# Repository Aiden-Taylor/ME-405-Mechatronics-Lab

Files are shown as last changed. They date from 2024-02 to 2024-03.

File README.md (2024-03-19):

# ME 405 Term Project
### Authors: Aiden Taylor, Jack Foxcroft, Julia Fay
For our ME 405 term project we have designed a tracking and triggering system for a Nerf gun that utilizes two servo motors and a thermal camera to hit a target. These components were controlled by a Nucleo STM32L476 microcontroller, and the software was coded in Python and micropython. This design was to be used for educational purposes by students of ME 405. The purpose of the Nerf gun system was to participate in a duel against similar systems designed by classmates. Two participants were to stand behind their Nerf gun, move around for five seconds, and freeze while the opponent's gun tried to shoot them. Our system was ultimately successful in aiming, triggering, and hitting our opponent.

## Hardware and Mechanical Design
The turret hardware consists of a Nucleo STM32L476RG, and an adapter board, the “Shoe of Brian” which adds additional features to the Nucleo necessary for our project. To allow controlled actuation and triggering of the turret we employed two DC motors and encoders lent to us by the ME 405 lab and an infrared camera to sense the thermal signature of our target and calculate the setpoint for our aiming motor.
The mechanical design consists of 3D-printed gears, bearings, a baseplate, motor mounts, and a fixture to house the Nerf gun. The CAD model of the system is shown below with details regarding each component of the system and their purpose.

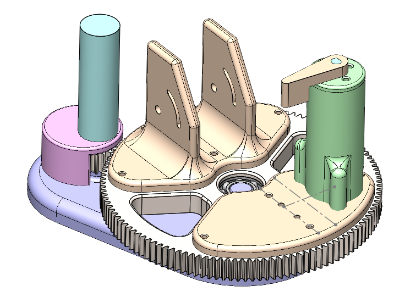
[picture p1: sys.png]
mechanical


**Figure 1:** Turret CAD Model

The gear ratio of our system is 6:1 and was designed to allow the turret to spin 180 degrees in one second. Overall, our design was made to be as simple and compact as possible while still being able to meet the requirements of the project.

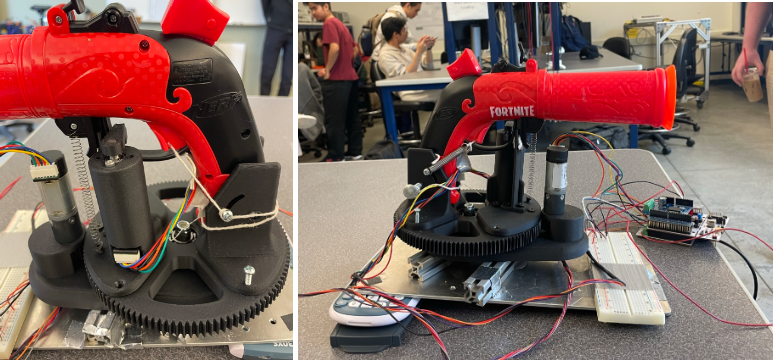
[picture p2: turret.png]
irlsys


**Figure 2:** Fully assembled turret with aiming and triggering subsystems.

To aid in providing the necessary force to engage the trigger mechanism, the team added a spring-tensioned string through the bottom portion of the trigger. Thus, when the servo moved the triggering lever, the trigger would engage consistently. A barrel support piece was added to aid in the gun's stability. Another spring was used to keep the gun secured on this support piece as seen in the left image above.

## Software Overview
The software for controlling the turret system was written in micropython such that it could be uploaded and run on the Nucleo. The team used a priority scheduler to efficiently run each task in the order of most time-sensitive to least time-sensitive. A generator function was used to generate effective multitasking between different system tasks. An in-depth coverage of the software can be found at the Doxygen page for this project https://aiden-taylor.github.io/ME-405-Mechatronics-Lab/

## Results
Our design was successful in tracking a target and shooting them after 5 seconds of the duel being initiated. However, we only produced this result once during our duel. We ran into some issues with the hardware, such as the wiring getting caught in the gears during the duel. We also missed our target two times. We tested our system at multiple stages in the project. Before we tested our FSM on the fully built system, we used the motors with flywheel attachments in the lab to ensure we were getting the expected outcome. Once the two motors were properly operating, we built the whole system and tested the full operation. This stage of testing included tuning the values of Kp for both the panning motor and the trigger motor. We aimed to minimize overshoot for the panning motor and ensure a large enough PWM signal was being sent to the trigger motor. Additionally, we adjusted the calculation for getting the position of the target from the thermal camera's output and converting this to how many degrees to turn the panning motor. To do this, we had to take into account that the thermal camera was closer to the target than the gun, and thus had a different angular relationship to the target than the gun. Improvements that could be made to the system to yield a more consistent outcome will be discussed in the next section.

## Takeaways and Recommendations
Overall, this project was very informative in terms of how to effectively implement a FSM in Python while utilizing a priority scheduler. You have to make sure that the period of your tasks is less than the period specified in the scheduler to ensure the correct operation. Also, the priority of the tasks must be balanced such that each task will have the chance to run. Having too high of a priority for a task may result in that task being run exclusively. Also, the team learned how to currently utilize shares. To ensure only one value was stored in each of the queues, the queue was cleared, and then restored at each instance of using the queue. This allowed us to avoid issues with grabbing an incorrect previous value for a share. 

In terms of the mechanical design of the system, several things could be improved upon. The budget for our system led us to the use of 3D printed parts which was a limiting factor in the mechanical operation. We used PLA to print the baseplate and had permanent shafts designed into the part which sheared off immediately after assembling the gears. To better improve this we suggest making the shafts separate parts made of stronger materials less prone to shearing.

We also noticed that the system was very prone to high friction and thus responded slower to inputs from our controller. To decrease system friction we recommend using higher-performance bearings, steel shafts, higher tolerance manufacturing of the baseplate for center-to-center distance of the gears, and snap rings to retain the gears and ensure correct alignment.

The system was also prone to missing its target which was the cause of many different issues. In our duel, we had five chances to aim, trigger, and shoot our target. We only hit our target one out of the five times, the system missed its target twice, a piece of string used to pre-load the trigger caught in the gears, and our trigger motor wire caught in the gears. In order to remedy these issues we recommend implementing better and more organized wire/string management to ensure the gears are left free to spin. To solve the aiming issue we recommend creating a more robust process in setting up the turret’s initial position and angle as well as the camera position and angle in reference to the turret and target.

The triggering mechanism also had its fair share of issues, mainly stemming from the torque required to trigger the Nerf gun. We recommend either using some sort of mechanical leverage to trigger the gun or selecting a higher torque servo motor for triggering to increase the repeatability of this system.

One software system that would be really interesting to implement would be real-time tracking. Our system takes one image of the target and calculates a setpoint based on the distance to the target, and the image column that the target was identified in. However, this required us to take the image after the target had stopped moving (after the five seconds had elapsed) to make certain that the setpoint calculated was correct. If real-time tracking was implemented, we might be able to calculate new setpoints every second or quicker to trigger the Nerf gun before the 5 seconds were up.

## Task Diagram and FSMs
### Task Diagram
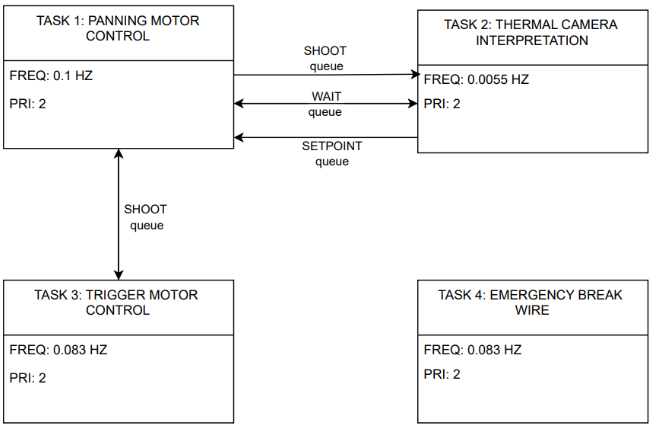
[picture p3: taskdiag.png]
tdiag


### Task 1 Finite State Machine
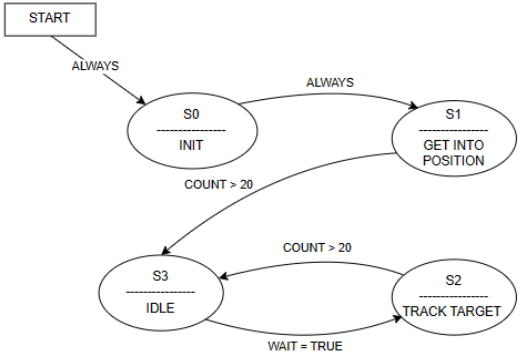
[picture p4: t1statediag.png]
t1diag


### Task 2 Finite State Machine
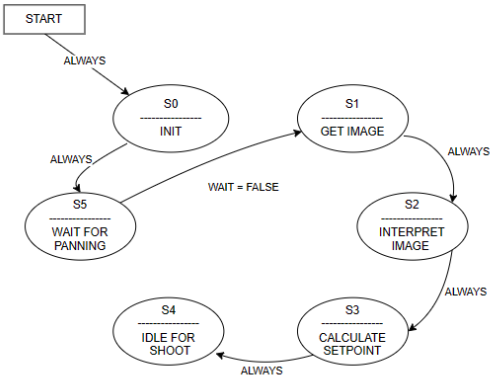
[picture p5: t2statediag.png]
t1diag


### Task 3 Finite State Machine
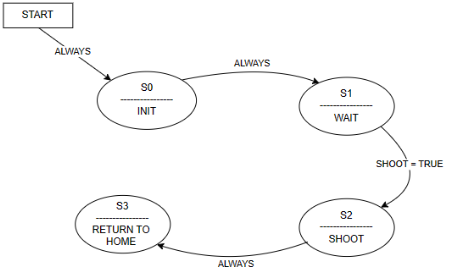
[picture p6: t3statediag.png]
t1diag


### Task 4 Finite State Machine
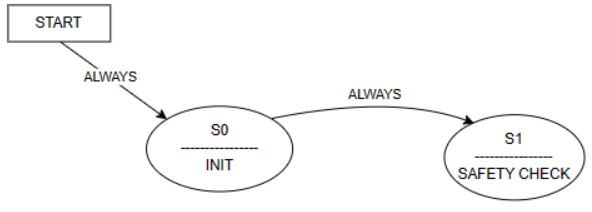
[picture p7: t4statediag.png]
t1diag


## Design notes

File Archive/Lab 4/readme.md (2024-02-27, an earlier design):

**README FOR THE BEST ME405 GROUP EVER**

*Authors: Aiden Taylor, Jack Foxcroft, Julia Fay*

~~Don't steal our code, or else you will be severly punished.~~

This GitHub is a compilation of all current code that has been written for ME405 Lab. The archive folder contains past lab code, while src contains the current lab's working code, the docs folder contains the documentation for the current lab, and the Doxyfile contains the Doxygen configuration.

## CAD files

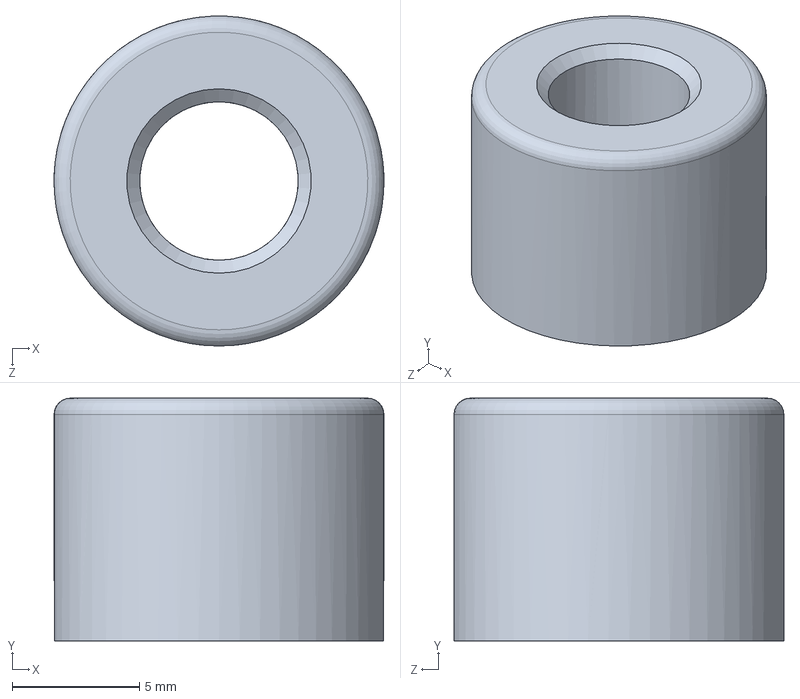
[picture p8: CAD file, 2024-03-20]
CAD/shaft.SLDPRT
13.0 x 9.53 x 13.0 mm

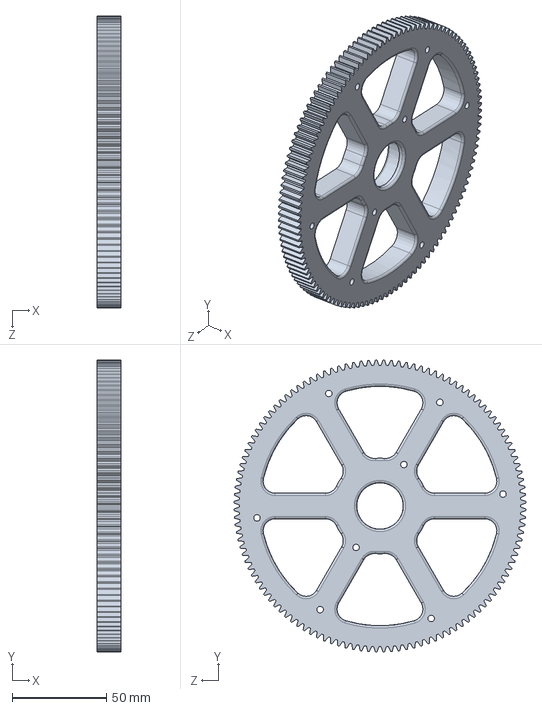
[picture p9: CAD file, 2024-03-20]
CAD/spur gear.SLDPRT
12.7 x 154.9 x 154.9 mm

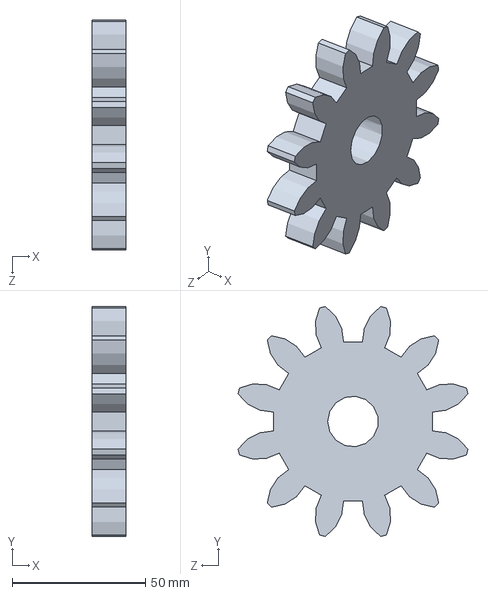
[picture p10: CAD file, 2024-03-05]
CAD/pinion.SLDPRT
12.7 x 86.4 x 86.4 mm

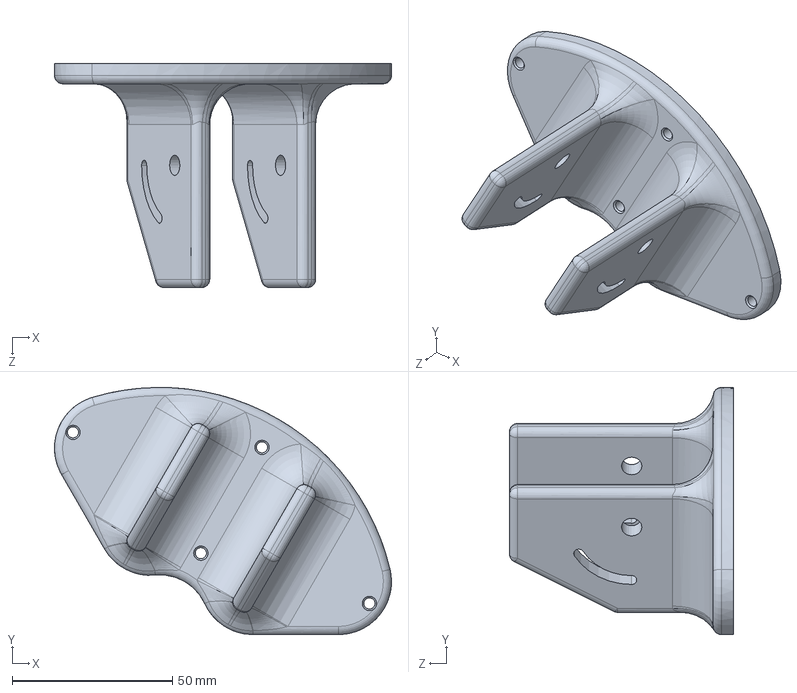
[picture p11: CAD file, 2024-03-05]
CAD/gun mount.SLDPRT
105.0 x 77.0 x 69.8 mm

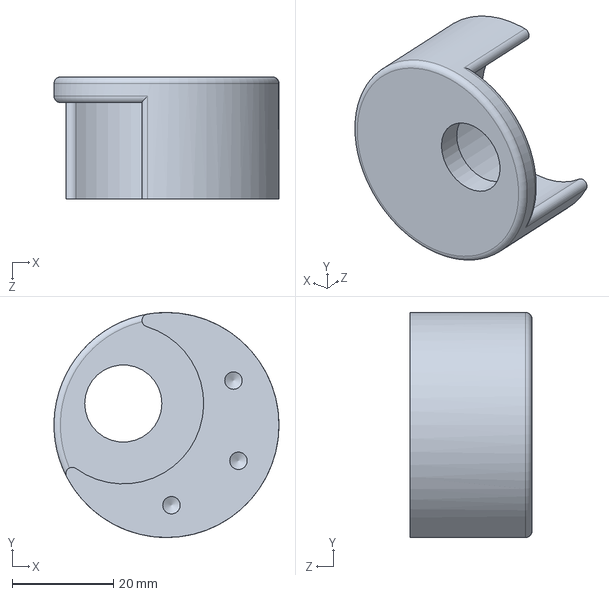
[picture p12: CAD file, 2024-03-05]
CAD/motor mount.SLDPRT
44.4 x 44.5 x 24.1 mm

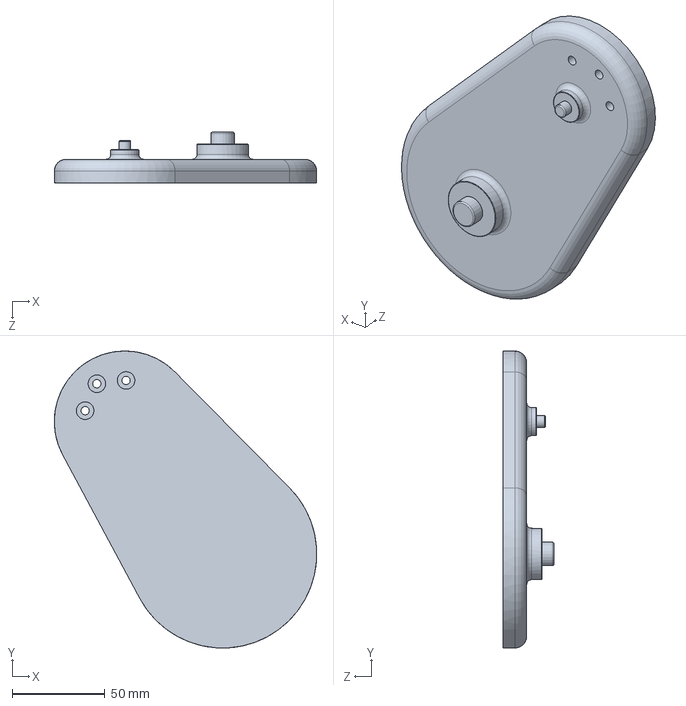
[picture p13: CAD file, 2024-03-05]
CAD/base.SLDPRT
141.7 x 160.4 x 27.3 mm

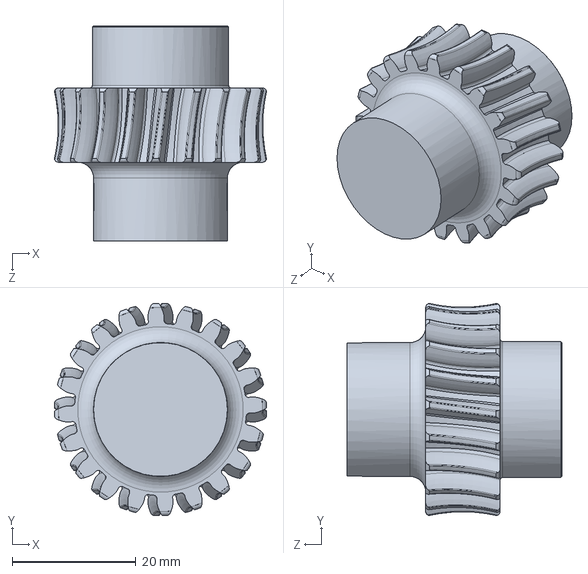
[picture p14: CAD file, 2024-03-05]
CAD/Part1.SLDPRT
34.2 x 34.2 x 34.7 mm

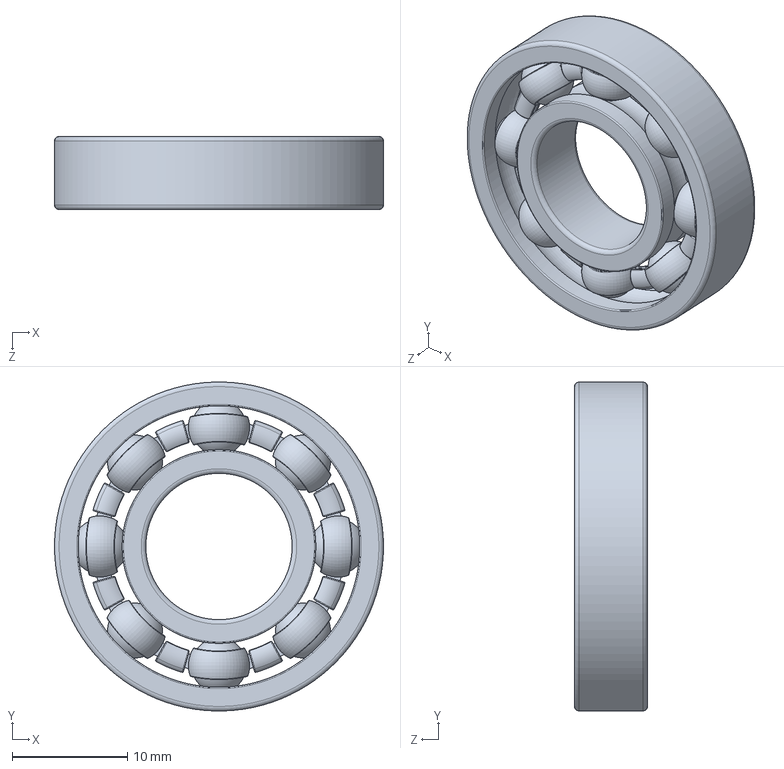
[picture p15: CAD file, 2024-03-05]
CAD/60355K173_Ball Bearing BIG.SLDPRT
28.6 x 28.6 x 6.35 mm

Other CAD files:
CAD/60355K173_Ball Bearing.SLDPRT

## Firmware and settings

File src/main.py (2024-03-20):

"""!
@mainpage Software Overview

@section intro_sec Introduction

This main page covers the workings of the main.py file used for this project, as well as the files that were used to make the whole system work.

@section file_sec Files

This is an overview of the files that we wrote and utilized:

@subsection controller_sec controller.py

This file is used as a high-level proportional controller for our motors. We use it to control the desired position of our motors, and also to interface with some of the lower-level files, seen below.

@subsection csv_sec csv_reader.py

This file was originally used for a plotter, but for the purposes of this project we adapted it to read the output of the thermal camera. We wrote a method in the class that reads the camera data, and then calculates the hottest thermal column, which is what we used to pick an aiming point.

@subsection encoder_sec encoder_reader.py

This file is a fairly self-explanatory class. We use it to read from the encoders and handle all the calculations related to determining the position of the motors. This file is referenced by the controller to read the motor positions.

@subsection mlx_sec mlx_cam.py

This is a file that was provided to us to read the infrared camera output. It was utilized in Task 2 of our main file.

@subsection motor_sec motor_driver.py

This file is used to control the speed of the motors. It takes a desired pwm output and feeds it to the motor driver. This file is also referenced by the controller, which uses this file and the encoder reader to create an effective proportional controller.

@section task_sec Tasks

IMAGE_PATH = my_image_dir

@image html taskdiag.png

The following are the tasks and states used in the main file of this project:

@subsection t1_sec Task 1

@image html t1statediag.png

Task 1 runs the panning motion for motor #1. This task first moves the turret into the 
    aiming position (180 degrees from initial position). Then, updates the panning motor 
    setpoint calculated by the thermal camera and runs until the PWM signal falls below 50%
    for more than 20 cycles and sets the panning motor duty cycle to 0 and waits for the trigger
    motor to complete its task. These are the states that are utilized in Task 1:

@subsubsection t1s0_sec State 0

This state is an initialization state for the panning motor that sets up the enable, pwm, and encoder pins, as well as
    establishing the controller class instance for the pan.

@subsubsection t1s1_sec State 1

This state is used to capture an image. Once that is completed, we move to state 2.

@subsubsection t1s2_sec State 2

This state is used when the turret is panning to track the target. In this current implementation of our code, we are not actively tracking 
    a target, we are instead waiting for the 5 seconds and then turning towards the target and firing. If we wanted to implement active
    tracking in the future, this state is ready for that, with a few modifications.

@subsubsection t1s3_sec State 3

This state is an idle for the panning motor. This is used both when we are tracking the duel target, and when we are waiting for our turret to fire



@subsection t2_sec Task 2

@image html t2statediag.png

Task 2 deals with the thermal camera. It initializes the camera's i2c communication
    protocal them waits until the panning motor completes its initial movement to the aiming position
    180 degrees from the initial postion. Then wait 3.25 seconds and get the image.
    Then, using the csv_reader class, calculate the column with the maximum summed thermal
    signature and calculate the setpoint based on the column. These are the states that are utilized in Task 1:

@subsubsection t2s0_sec State 0

This state is an initialization state for the camera that intitializes the mlx_cam class instance, as well as setting the refresh rate of the camera.

@subsubsection t2s1_sec State 1

This state is used to spin the whole turret 180 degrees at the start of the duel. Once it has turned, it switches to state 3.

@subsubsection t2s2_sec State 2

This state utilizes the csv reader to interpret the data that was captured by the camera in state 1. This gives us a column from the data that we need to
    aim at. This moves us to state 3.

@subsubsection t2s3_sec State 3

This state takes the data that we got from the csv reader and uses trigonometry and information about our camera and setup geometry to calculate the angle 
    that our turret needs to turn to correctly aim at the target, and then it uses a shared variable to pass that information to Task 1 and 3.
    
@subsubsection t2s4_sec State 4

This state waits for the turret to fire and does not take any images that may cause lag.

@subsubsection t2s5_sec State 5

This state waits for the panning motor to spin 180 degrees at the start of the duel before taking any images.

    
@subsection t3_sec Task 3

@image html t3statediag.png

Task 3 runs the trigger motion for the motor #2. First, task 3 waits until the panning
    motor reaches the setpoint calculated by the thermal camera. Then, it runs the trigger motor
    to a setpoint of 30 degrees, then returns to its intial position. The states it uses are below:

@subsubsection t3s0_sec State 0

This state is an initialization state for the trigger motor that sets up the enable, pwm, and encoder pins, as well as
    establishing the controller class instance for the trigger.

@subsubsection t3s1_sec State 1

This state is used to wait until the turret is ready to fire

@subsubsection t3s2_sec State 2

This state is used when the turret is firing. This activates the trigger motor to pull until it reaches the desired setpoint that we 
    tested to guarantee that the turret fires.

@subsubsection t3s3_sec State 3

This state returns the trigger mechanism to its zero location after firing.

@subsection t4_sec Task 4

@image html t4statediag.png

Task 4 is a simple task that acts as our safety system. Our design used a safety wire that when pulled, shuts down the whole system. The states used are as follows:

@subsubsection t4s0_sec State 0

This state simple initializes the variables used for the safety wire.

@subsubsection t4s1_sec State 1

This state is where the safety task always operates after initialization. It checks that the wire is still connected. If the wire is pulled, then the system is halted and will no longer
    operate until it is reset and the safety wire is replaced.

@file main.py

This is the main file for the term project. 

@author Aiden Taylor, Jack Foxcroft, Julia Fay
@date   2024-Mar-18
"""


#import all relevant modlues and files 
import gc
import pyb
import cotask
import task_share
import controller
import utime
import mlx_cam
import csv_reader
import math

#create global variable done 
global done
done = False 

def task1_fun(data):
    """!
    Task 1 runs the panning motion for motor #1. This task first moves the turret into the 
    aiming position (180 degrees from initial position). Then, updates the panning motor 
    setpoint calculated by the thermal camera and runs until the PWM signal falls below 50%
    for more than 20 cycles and sets the panning motor duty cycle to 0 and waits for the trigger
    motor to complete its task
    
    @param data The tuple used to store all shared variables between tasks
    """
    setpoint_share, shoot_share, wait_share = data  # Access shared variables from data tuple
    t1_state = 0; 
    
    print("Starting task 1")
    
    while True:
        

        shoot = shoot_share.get()  # Get shoot flag from shared variable
        wait = wait_share.get()
        wait_share.put(wait)
        
        # Implement FSM inside while loop
        #S0 - MOTOR INIT 
        #Initialize motor pins, Kp value, and position 
        if (t1_state == 0):
            # Run state zero code
            print("Task 1 state: ", t1_state)
            print("Initializing panning motor and encoder")
            ena = pyb.Pin.board.PC1
            in1 = pyb.Pin.board.PA0
            in2 = pyb.Pin.board.PA1
            motimer = 5

            #encoder init
            cp1 = pyb.Pin.board.PC6
            cp2 = pyb.Pin.board.PC7
            cptimer = 8
            Kp_init = 10
            setpoint = 0
            setp_init = 0       #   FIGURE OUT WHAT TO SET THIS TO FOR EACH MOTOR
      

            #establish controller object
            global var
            var = controller.P_Control(Kp_init, setp_init, 0, motimer, ena, in1, in2, cp1, cp2, cptimer)

            #zero the encoder count and position
            var.zero()
            var.set_Kp(Kp_init)
            global timtimeint
            timtimeint = utime.ticks_ms()
            var.moe.set_duty_cycle(0)
            #make sure the queue only has one value  
            wait_share.get()
            wait_share.put(True)
            count = 0

            #always go to state 1 from init  
            t1_state = 1   


        #S1 - GET INTO POSITION     
        elif (t1_state == 1):
            print("In the process of moving 180")
            #create the 180 degree setpoint (180 degrees, w/ a gear ratio of 6:1 so 6*180)
            one_eighty = 6*180
            var.run(one_eighty,timtimeint)
            print("Task 1 state: ", t1_state)
            
            #Check if the motor has reached this new position by checking if the PWM 
            #signal stays below 20 at least 10 times 
            if abs(var.get_PWM()) < 50:
                count += 1
            if count > 20: 
                print("I moved 180!")
                #turn off trigger motor
                var.moe.set_duty_cycle(0)
                #clear the queue and put False  
                wait_share.get()
                wait_share.put(False)
                #always go to the Idle state 3 to wait for the camera image to be taken 
                t1_state = 3
                #reset the count to zero 
                count = 0
                var.set_Kp(5)
                #zero the encoder position 
                var.zero()

        
        #S2 - TRACK TARGET    
        elif (t1_state == 2): 
            print("Task 1 state: ", t1_state)    
                    
            setpoint = setpoint_share.get()  # Get setpoint from shared variable
            setpoint_share.put(setpoint)     # Make sure the queue stays neutral
            print(f"updating setpoint is: {setpoint}")
           
            #update the motors setpoint and run 
            var.run(setpoint, timtimeint)
            
            #Check if the motor has reached this new position by checking if the PWM 
            #signal stays below 50 at least 20 times 
            if abs(var.get_PWM()) < 50:
                count += 1

            if count > 20:
                print("I moved to new setpoint!")
                #turn off trigger motor
                var.moe.set_duty_cycle(0)
                #clear the queue and put False  
                wait_share.get()
                wait_share.put(False)
                #go to the Idle state 3 to shoot 
                t1_state = 3
                #reset the count to zero 
                count = 0
                #zero the encoder position 
                var.zero()
                #tell the world its time to shoot 
                shoot_share.get()
                shoot_share.put(True)
    
            
        #S3 - IDLE     
        elif (t1_state == 3):
            print("Task 1 state: ", t1_state)
            print("Panning motor idling to shoot or take camera image")
            #set duty cycle to 0 to stop the motor 
            var.moe.set_duty_cycle(0)
            #if the trigger has shot its shot, return back to state 2 
            if wait == True: 
                t1_state = 2
                

        else:
            # If the state isnt 0, 1, 2, or 3 we have an
            # invalid state
            raise ValueError('Invalid state')
            
        print("Exiting task 1")
        yield 0


def task2_fun(data):
    """!
    Task 2 deals with the thermal camera. It initializes the camera's i2c communication
    protocal them waits until the panning motor completes its initial movement to the aiming position
    180 degrees from the initial postion. Then wait 3.25 seconds and get the image.
    Then, using the csv_reader class, calculate the column with the maximum summed thermal
    signature and calculate the setpoint based on the column.
    
    @param data The tuple used to store all shared variables between tasks
    """
    
    t2_state = 0
    setpoint_share, shoot_share, wait_share = data  # Access shared variables from data tuple
    print("Starting task 2")
       
    while True:
        # Implement FSM inside while loop
        
        #S0 - CAMERA INIT 
        if t2_state == 0:
            print("Task 2 state: ", t2_state)
            print("Initializing thermal camera") 
            #Initialize camera object 
            i2c_bus = mlx_cam.I2C(1)
            # Select MLX90640 camera I2C address, normally 0x33, and check the bus
            i2c_address = 0x33
            scanhex = [f"0x{addr:X}" for addr in i2c_bus.scan()]
            # Create the camera object and set it up in default mode
            gc.collect()
            camera = mlx_cam.MLX_Cam(i2c_bus)
            print(f"Current refresh rate: {camera._camera.refresh_rate}")
            camera._camera.refresh_rate = 10.0
            print(f"Refresh rate is now:  {camera._camera.refresh_rate}")
            image = None
            gc.collect()
            
            #always go to state 5 to wait for the panning motor to move 180 degrees 
            t2_state = 5      
            #initialize shoot to be false  
            shoot = False
        
        #S1 - GET CURRENT IMAGE     
        elif t2_state == 1: 
            print("Task 2 state: ", t2_state)
            print("Getting current image")
            print("Click.", end='')
            
            #zero the encoder to base the new setpoint calc off of the 
            #zeroed current position 
            var.zero()
            
            #init image to be none for the non blocking get image function 
            image = None
            begintime = utime.ticks_ms()
            utime.sleep(3.25)
            # Use non blocking code 
            while not image:
                image = camera.get_image()
                yield t2_state 
            print(f" {utime.ticks_diff(utime.ticks_ms(), begintime)} ms")
            
            #always go to state 2 to interpret image 
            t2_state = 2
            
        #S2 - INTERPRET IMAGE 
        elif t2_state == 2: 
            print("Task 2 state: ", t2_state)
            print("Interpreting image")
            #convert the image to CSV format 
            reed = csv_reader.CSV(camera.get_csv(image, limits=(0, 99)))
            #use the readdata() function to calculate the column with the highest 
            #thermal values 
            reed.readdata()
            #extract the column and total value and print 
            col, total = reed.col_largest()
            print("COLLUMN", col,"TOTAL", total)
            #always go to state 3 to calculate the new setpoint 
            t2_state = 3       
            
        #S3 - CALCULATE NEW SETPOINT 
        elif t2_state == 3: 
            print("Task 2 state: ", t2_state)
            print("Calculating new setpoint")
           
            # Camera FOV = 55 degrees x 35 degrees
            # Gear Ratio = 6:1
            # Our motors current position is the center of the frame, so column 16 
            # If we want to make the col with the highest total heat value the new center of the frame 
            # Then we have to calculate how many degrees it takes to reach that position 
            # 1 pixel = 1.72 degrees
            # Resolution = 32 x 24 pixels 
            #adjust for the trig of the table
            dist_from_table_edge = 4.5/12
            x = 8-dist_from_table_edge
            #trig_adjustment = math.atan(4.2/(8+x))/27.5 
            trig_adjustment = 0.5
            degs = (col-16)*1.72*trig_adjustment 
            #multiply degree value by 6 to account for the gear ratio and pring 
            new_setpoint = int(degs * 6)  
            print("The new setpoint is", new_setpoint)
            #update the shares values 
            setpoint_share.get()
            setpoint_share.put(new_setpoint)
            wait_share.get()
            wait_share.put(True)
            print("Updated the motor angle")
            shoot = False
            shoot_share.get()
            shoot_share.put(shoot)
            #always go to state 4 Idle for shoot since target has been found and new setpoint identified. 
            t2_state = 4 

        #S4 - IDLE FOR SHOOT  
        elif t2_state == 4: 
            print("Task 2 state: ", t2_state)
            print("Camera Idling to shoot")

        #S5 - WAIT FOR PANNING 
        elif (t2_state == 5):
            print('Waiting for panning motor to reach previous setpoint')
            #wait for it to spin to the current desired setpoint, and then transition to state 1
            wait = wait_share.get()
            wait_share.put(wait)
            if wait == False:
                t2_state = 1  
                
        else:
            # If the state isnt 0, 1, 2, 3, 4 or 5 we have an
            # invalid state
            raise ValueError('Invalid state')

        print("Exiting task 2")    
        yield 0
            
def task3_fun(data):
    """!
    Task 3 runs the trigger motion for the motor #2. First, task 3 waits until the panning
    motor reaches the setpoint calculated by the thermal camera. Then, it runs the trigger motor
    to a setpoint of 30 degrees, then returns to its intial position.

    @param data The tuple used to store all shared variables between tasks
    """
    t3_state = 0; 
    print("Task 3")
    
    setpoint_share, shoot_share, wait_share = data  # Access shared variables from data tuple

    while True:
        
        # Implement FSM inside while loop
        #S0 - MOTOR INIT  
        if (t3_state == 0):
            print("Task 3 state: ", t3_state)
            print("Initializing trigger motor and encoder")
            
            #Initialize motor pins, Kp value, and position
            ena = pyb.Pin.board.PA10
            in1 = pyb.Pin.board.PB4
            in2 = pyb.Pin.board.PB5
            motimer = 3

            #encoder init
            cp1 = pyb.Pin.board.PB6
            cp2 = pyb.Pin.board.PB7
            cptimer = 4
            trigger_Kp_init = 20
            setp_init = 360
            count2 = 0

            #establish controller class
            global var2
            var2 = controller.P_Control(trigger_Kp_init, setp_init, 0, motimer, ena, in1, in2, cp1, cp2, cptimer)

            #set the Kp value 
            Kp_init = 25
            
            #zero the encoder count and position
            var2.zero()
            var2.set_Kp(Kp_init)
            timtimeint = utime.ticks_ms()

            #start the motor off as unmoving 
            var2.moe.set_duty_cycle(0)
            
            #always go to state 1
            t3_state = 1
            
        #S1 - WAIT 
        elif (t3_state == 1):
            print("Task 3 state: ", t3_state)
            print("Trigger motor waiting to shoot")
            var2.moe.set_duty_cycle(0)
            
            shoot = shoot_share.get()  # Get shoot flag from shared variable
            shoot_share.put(shoot)     # Put shoot back in so that Task 1 can get it
            #if shoot is true go to the shoot state 
            if shoot == True: 
                t3_state = 2 
                
        #S2 - SHOOT 
        elif (t3_state == 2): 
            print("Task 3 state: ", t3_state)
            print("Time to shoot!")
            
            #create the setpoint such that the trigger moves the corrent distance 
            #estimate to be 30 degrees  
            trigger_sp = 30   
            #run the motor 
            var2.run(trigger_sp, timtimeint)
            #if the motor has a low PWM value, assume it has reached its position 
            if var2.get_PWM() < 0: 
        
                #turn off trigger motor 
                var2.moe.set_duty_cycle(0)
                #always go to state 3 to return the trigger to its origonal posisiton 
                t3_state = 3
                #initialize count2 to be zero for the next state 
                count2 = 0
                #zero encoder count for the next state
                var2.zero()
                #set shoot to be False since we are done shooting 
                shoot = False 
                shoot_share.get()
                shoot_share.put(shoot)
                
        #S3 - RETURN TRIGGER MECHANISM
        elif (t3_state == 3): 
            print("Task 3 state: ", t3_state)
            print("Return Trigger")
            var2.set_Kp(2)
            #create the setpoint such that the trigger moves the corrent distance 
            #estimate to be half a revolution   
            trigger_sp = -30
            #get current clock count 
            #timtimeint = utime.ticks_ms()
            #run the motor 
            var2.run(trigger_sp, timtimeint)
            #if the motor has a low PWM value, assume it has reached its position 
            if abs(var2.get_PWM()) < 20: 
                count2 += 1
            if count2 > 15:
                #turn off trigger motor 
                var2.moe.set_duty_cycle(0)
                t3_state = 1
                global done
                done = True
 
        else:
            # If the state isnt 0, 1, 2 or 3 we have an
            # invalid state
            raise ValueError('Invalid state')
        
        print("Exiting task 3")      
        yield 0
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

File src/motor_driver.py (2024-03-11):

"""! @file motor_driver.py
  
  This file is responsible for implementing the speed control for a motor using a PWM signal that 
  can be modified based on the users input. This file can be used on multiple motors in a main 
  file at the same time as it takes the motor pins as an input. 

  @author Aiden Taylor, Julia Fay, Jack Foxcroft
  
  """

#import relevant modules 

import pyb 
import micropython

micropython.alloc_emergency_exception_buf(100)

class MotorDriver:
    """! 
      This class implements a motor driver for an ME405 kit. 
      """

    def __init__ (self, en_pin, in1pwm, in2pwm, timer, enapin, motorpin1, motorpin2):
        """! 
        Creates a motor driver by initializing GPIO
        pins and turning off the motor for safety. 
        @param en_pin The value sent to the enable pin controlled by the microcontroller. When the en_pin
               is set high, it enables the motor. 
        @param in1pwm The initial pwm percentage value sent to the timer 
               channel corresponding to the first motor pin. When in1pwm 
               is set to 0, the motor runs in the forward direction.  
        
        @param in2pwm The initial pwm percentage value sent to the timer 
               channel corresponding to the second motor pin. When in2pwm 
               is set to 0, the motor runs in the reverse direction. 
        
        @param timer The timer channel that corresponds with the motor pins 
               used for the motor. 
        
        @param enapin The chosen enable pin number controlled by the microcontroller corresponding 
               to EN_A/OCD_A or EN_B/OCD_B on the L6206. 
        
        @param motorpin1 The first chosen motor pin on the CPU corresponding to the IN1 A/B pin 
               on the L6206.
        
        @param motorpin2 The second chosen motor pin on the CPU corresponding to the IN2_A/B pin 
               on the L6206.
        
        """

        #set pin as an output for ENA/OCD and set as open-drain outputs with pullup resistors enabled
        self.ena_pin = pyb.Pin((enapin), pyb.Pin.OUT_OD, pyb.Pin.PULL_UP)
        self.ena_pin.value(en_pin)

        #set pin as an output for IN1A
        self.m_pin1 = pyb.Pin((motorpin1), pyb.Pin.OUT_PP)

        #set pin as an output for IN2A
        self.m_pin2 = pyb.Pin((motorpin2), pyb.Pin.OUT_PP) 

        #create timer on channel 1 to work with pin for PWM for the motor
        self.tim = pyb.Timer(timer, freq=20000)
        self.ch1 = self.tim.channel(1, pyb.Timer.PWM, pin=self.m_pin1)
        self.ch1.pulse_width_percent(in1pwm)

        #create timer on channel 2 to work with pin for PWM for the motor
        self.ch2 = self.tim.channel(2, pyb.Timer.PWM, pin=self.m_pin2)
        self.ch2.pulse_width_percent(in2pwm)

        print ("Creating a motor driver")

    def set_duty_cycle(self, level):
       """!
       This method sets the duty cycle to be sent
       to the motor to the given level. Positive values
       cause torque in one direction, negative values
       in the opposite direction.
       @param level A signed integer holding the duty
              cycle of the voltage sent to the motor 
       """
       
       self.ena_pin.value(1) #sets the enable pin high 
       print(f"Setting duty cycle to {level}")
       if level > 0:
              self.ch1.pulse_width_percent(0)
              self.ch2.pulse_width_percent(level)
       
       else:
              level = level*-1
              self.ch1.pulse_width_percent(level)
              self.ch2.pulse_width_percent(0)
       
       
       
       
    
if __name__ == "__main__":
    # Script code goes here
    enpin = 0
    a_pin = 0
    another_pin = 0
    a_timer = 3
    enp1 = pyb.Pin.board.PC1
    mp2 = pyb.Pin.board.PA0
    mp3 = pyb.Pin.board.PA1
    moe = MotorDriver(enpin, a_pin, another_pin, a_timer, enp1, mp2, mp3)
    while True:
        moe.set_duty_cycle(int(input('set a duty cycle')))
        # moe.set_duty_cycle(0)

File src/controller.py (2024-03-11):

"""! @file controller.py
  
  This file controls the speed of the motor by first comparing the actual position of the 
  motor and the desired position of the motor. This error value is multiplied by a constant
  Kp that is specified by the user. This calculation is then used to determine the PWM 
  signal that is sent to the motor. 
  
  @author Aiden Taylor, Julia Fay, Jack Foxcroft
  """

#import relevant modules and files 
from motor_driver import MotorDriver
from encoder_reader import Encoder
import pyb
import utime

class P_Control(): 
    """! 
            This class implements P only motor control for a motor in the ME 405 kit. 
            """
    
    def __init__(self, in_Kp, in_setpoint, enapin, timer, enp1, mp1, mp2, coderp1, coderp2, codertimer):
        """!
        The initialization function inside the P_Control class initializes all key parameters for this class. 
        This includes inputs for the motor pins and encoder pins used in the encoder_reader and motor_driver 
        imported classes. Additionally, the setpoint and Kp values are initialized, as well as the time and 
        position arrays that will be used within the P_control class. 
        
        @param in_Kp The proportional gain constant used to calculate the PWM signal sent to the motor. 
        
        @param in_setpoint The setpoint value is the desired position of the motor. The 
               current position of the motor is compared to the setpoint to calculate the 
               error. 
        
        @param enp1 The value sent to the enable pin controlled by the microcontroller. When the en_pin
               is set high, it enables the motor. 
               
        @param in1pwm The initial pwm percentage value sent to the timer 
               channel corresponding to the first motor pin. When in1pwm 
               is set to 0, the motor runs in the forward direction.  
        
        @param in2pwm The initial pwm percentage value sent to the timer 
               channel corresponding to the second motor pin. When in2pwm 
               is set to 0, the motor runs in the reverse direction. 
        
        @param timer The timer channel that corresponds with the motor pins 
               used for the motor. 
        
        @param enapin The chosen enable pin number controlled by the microcontroller corresponding 
               to EN_A/OCD_A or EN_B/OCD_B on the L6206. 
        
        @param mp1 The first chosen motor pin on the CPU corresponding to the IN1 A/B pin 
               on the L6206.
        
        @param mp2 The second chosen motor pin on the CPU corresponding to the IN2_A/B pin 
               on the L6206.
               
        @param coderp1 The encoder pin on the L6206 corresponding to channel A for the encoder. 
        
        @param coderp2 The encoder pin on the L6206 corresponding to channel B for the encoder. 
        
        @param codertimer The timer chanel corresponding to the selected encoder pins.  
        
        """
        
        #initialize values for setpoint, gain
        self.setpoint = in_setpoint
        self.Kp = in_Kp

        self.times = []
        self.position = []
        
        #create encoder object 
        self.enco1 = Encoder(coderp1, coderp2, codertimer)
        
        #initialize variables for motor driver 
        self.in1_pin = 0
        self.in2_pin = 0

        #create motor driver object 
        self.moe = MotorDriver(enapin, self.in1_pin, self.in2_pin, timer, enp1, mp1, mp2)

       

    def run(self,in_setpoint, z_ticks):
        """!
            The run function in the P_Control class calculates the PWM signal that will be 
            sent to the motor by taking into accound the setpoint of the motor, and 
            the current position of the motor. These values are subtracted to find the 
            error which is then multiplied by Kp. If this value exceeds -100 or 100, the 
            value is saturated to either -100 or 100. Then the set_duty_cycle function 
            imported from the motor_driver class is run. The calculated PWM signal is 
            returned at the end of the funciton. 
            
            @return The PWM signal calcuated by the P control loop is returned. 
            """  
        self.setpoint = in_setpoint 
        encout = self.enco1.read()
        self.times.append(utime.ticks_diff(utime.ticks_ms(), z_ticks))
        self.position.append(encout)
        self.PWM = self.Kp * (self.setpoint - encout) 
        if self.PWM > 100:
            self.PWM = 100
        elif self.PWM < -100:
            self.PWM = -100   
        self.moe.set_duty_cycle(self.PWM)
        return(self.PWM)
        

    def get_PWM(self):
        return(self.PWM)
    

    def set_setpoint(self,in_sp):
        """!
            The set_setpoint function in the P_Control class sets the setpoint of the motor 
            that will be used to calculate the error in the run fuction. 
            """
        
        self.setpoint = in_sp

    def set_Kp(self,des_Kp): 
        """!
            The set_Kp function in the P_Control class sets the Kp value that will be used to
            calculate the PWM value in the run function. 
            """
        self.Kp = des_Kp 

    def zero(self):
        """!
            The zero function in the P_Control class runs the zero function from the imported 
            encoder_reader class. This function sets the timer count, motor position, prev_pos, 
            curr_pos, and delt to zero. This can be used to initialize the position of the motor. 
            """
        self.enco1.zero()

    def print_res(self):
        """!
            The print_res fucntion in the P_Control class prints the position and time data 
            of the motor in a csv format that can be easily read and plotted in a separate funciton. 
            """
        for i in range(len(self.times)):
            print(str(self.times[i]) + "," + str(self.position[i]))
        self.times = []

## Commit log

2024-01-29 we dont need this
    [data.csv]
2024-01-30 Lots Changes
    Fixed lab code, fixed broken doxygen, fixed otterly plot, should be perfectly functional
    [main.py, week2.py]
2024-02-21 Start of base plate
    [Base Plate.SLDPRT]
2024-02-27 set up i2c
2024-02-27 I2C labskeroony
2024-03-05 moving things around
    [Base Plate.SLDPRT]
2024-03-05 CAD Upload
    [60355K173_Ball Bearing BIG.SLDPRT, 60355K173_Ball Bearing.SLDPRT, Part1.SLDPRT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]
2024-03-09 added print statements to see where we are in the code for debugging
2024-03-11 Updates with shares and encoder reader
2024-03-20 Problem 16
    [shaft.SLDPRT, spur gear.SLDPRT]
